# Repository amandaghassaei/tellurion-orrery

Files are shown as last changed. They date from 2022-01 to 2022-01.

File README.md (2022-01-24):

# Tellurion Orrery

This is a repository of files related to building a tellurion (Earth, Moon, and Sun) orrery from scratch.  Please refer to my [Instructables post](https://www.instructables.com/Orrery-Earth-Moon-and-Sun/) for more information about how to make this project.

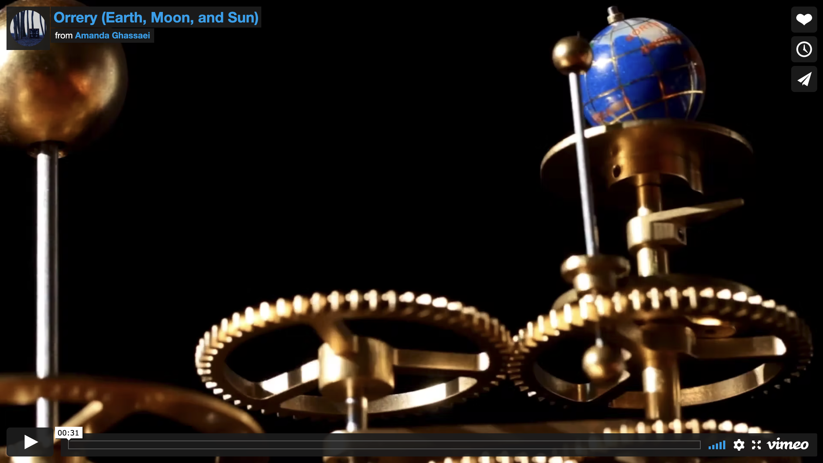
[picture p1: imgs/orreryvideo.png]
Orrery (Earth, Moon, and Sun) (https://vimeo.com/669322303 "Orrery (Earth, Moon, and Sun) - Click to Watch!")


### Repository Contents:

- [angled-jigs](angled-jigs) contains STL files for the 3D printed jigs used to cut angled holes in some parts.
- [bom](bom) contains an archived version of the bill of materials for the project, find the most up-to-date copy on [Google Docs](https://docs.google.com/spreadsheets/d/1O1LCT8TSBF-lglJqdujguVSw7xpgpI2WuT8ZgHCS0Z8/edit?usp=sharing).
- [cad](cad) contains archived versions of the cad files for the project and links to the most up-to-date versions online (see [cad/README.md](cad/README.md))
- [engravings](engravings) contains source code for generating three engravings used in the design, as well as generated DXF files.
- [gear-calculations](gear-calculations) contains information about how the mechanism was designed as well as source code for optimizing the gear ratios.
- [gear-depthing-gauge](gear-depthing-gauge) contains DXF files for laser cutting the body of the gear depthing gauge from acrylic.
- [laser-cutting](laser-cutting) contains vector files for laser cutting washers and other parts needed in the orrery design.

All files can be downloaded by clicking the green "Code" > "Download ZIP" button at the top of this page.

## License

All code and design files in this repo are free to use however you like (MIT License).

### Exceptions:

[engravings](engravings) contains a copy of [p5.js](https://github.com/processing/p5.js/), which is licensed under GNU.

[engravings/fonts](engravings/fonts) contains some fonts that likely have their own licenses associated with them.

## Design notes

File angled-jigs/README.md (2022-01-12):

## Angled Jigs

3D printed jigs for drilling angled holes in brass parts.  The most up-to-date jigs can be exported from the [CAD model](https://a360.co/3HCbeUA) (move the timeline to the end to uncover the jig designs).

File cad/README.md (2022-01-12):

## CAD Files

This directory contains archived Fusion360 files for the orrery and other associated designs; the most up-to-date CAD files can be found online:

- [Orrery v2](https://a360.co/3HCbeUA)
- [Shaft Cutting Jig](https://a360.co/3G0PzVP)
- [Gear Depthing Gauge](https://a360.co/31AS3LG)
- [Wood Cutting Layout](https://a360.co/3qWjdVE) (just a sketch, ignore warnings about empty model)

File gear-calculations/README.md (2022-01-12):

# Gear Calculations

The orrery design consists of 4 interconnected gear trains that control the relative motions of the earth, moon, and sun, and a fifth gear train that ticks forward a dial marking 100 years.

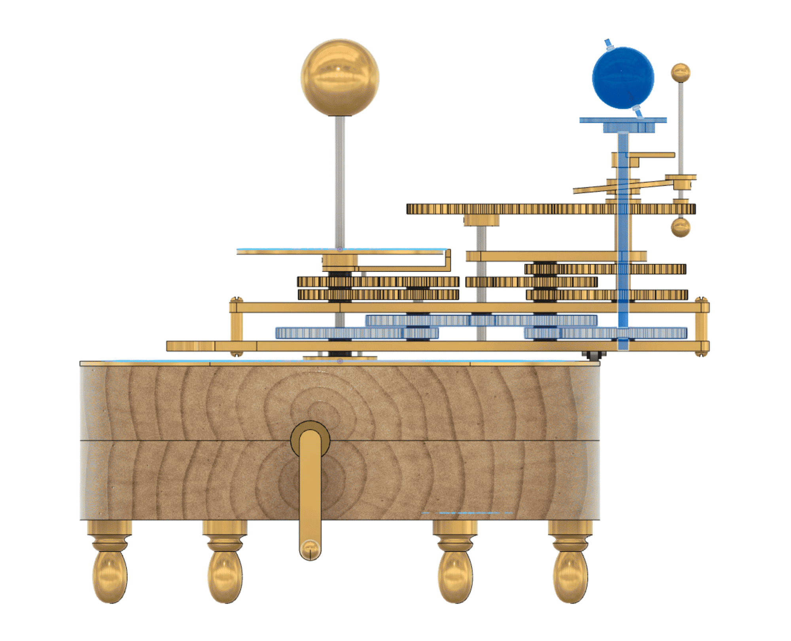
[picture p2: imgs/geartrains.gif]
5 gear trains


In addition to accurately positioning various components of the orrery, the gears must be sized so that they fit coaxially on five vertical axles:

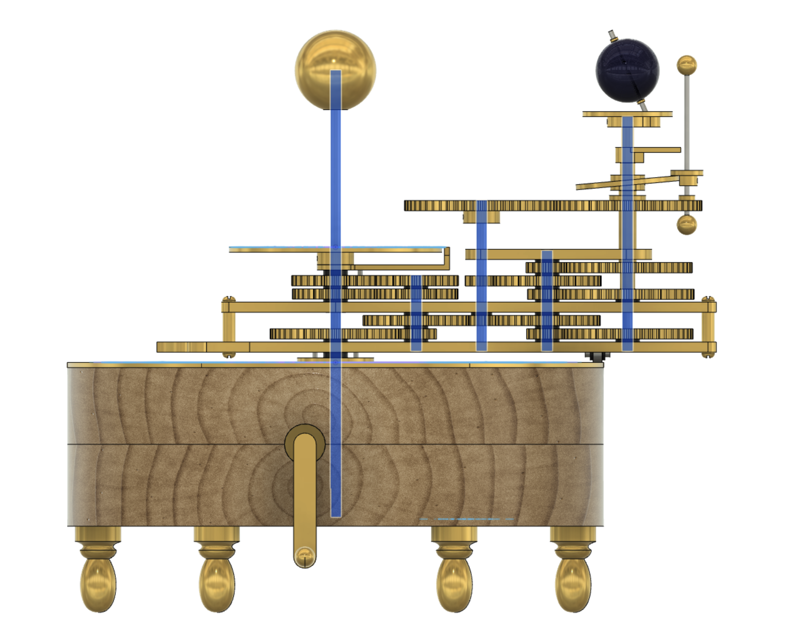
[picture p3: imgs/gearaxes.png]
gear axles


My code for calculating the gear ratios was done quickly without much thought for reuse – but I've added some notes here to explain the process.  

I've saved all the information I used during these calculations to a [Google Doc](https://docs.google.com/spreadsheets/d/1HO8HQtnuJBg7-cl2iLWuv1kIT8sFUn2m3BNM2MRiHnA/edit?usp=sharing) and I've backed up all the data in the [results](results) folder.  The first tab shows the astronomical parameters I was trying to model and their frequency.  Highlighted in blue are the gear parameters I used in v1 of my design, and highlighted in magenta are parameters used in v2 of my design.  The magenta and blue colors are continued across the other tabs in the sheet, where you can see more gear ratio options I was considering.

All the gear generation code was written in javascript and is included in this folder. I really liked this online [Gear Train app](http://scientific601.altervista.org/gear/gearcalc.html) and used it as a starting point as I began to design my gear trains, but found that I needed to calculate a large set of candidate gear trains for a given target ratio instead of just the single most optimal configuration. The file [GearCalculator.js](https://github.com/amandaghassaei/tellurion-orrery/blob/main/gear-calculations/GearCalculator.js) contains a function `calcGearTrain` that performs an exhaustive search to find set of gears meeting min tooth, max tooth, number of stages, and maximum error requirements (it takes about five minutes to complete for the three stage gear trains I'm looking at). The solutions (`hits`) are printed as a tsv to the console, so they can easily be copied and pasted into a spreadsheet.

### Moon Orbit

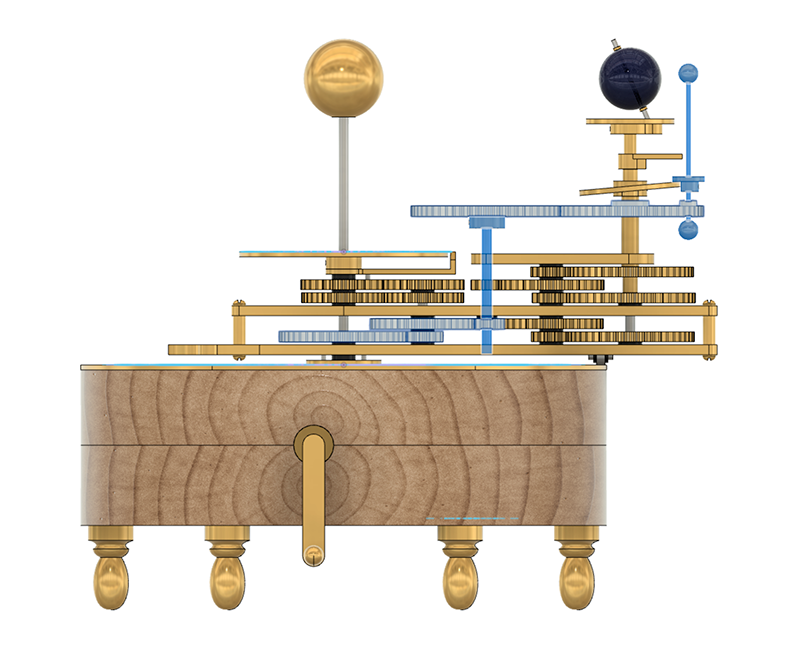
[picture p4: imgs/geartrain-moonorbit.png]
moon orbit gear train


First I used GearCalculator.js to calculate optimal solutions for a 3 stage gear train to drive the rotation of the moon around the earth. I chose a minimum tooth number of 8 and a maximum of 55. My code found the same optimal ratios as the online gear train app, but also gave me many alternatives that were slightly less optimal from an error perspective, but may satisfy other geometric properties of interest. I saved all permutations of each of these `hits` to a global variable called `options` in the file [ImportOptions.js](https://github.com/amandaghassaei/tellurion-orrery/blob/main/gear-calculations/ImportOptions.js).

[CalcFit.js](https://github.com/amandaghassaei/tellurion-orrery/blob/main/gear-calculations/CalcFit.js) uses the information stored in `options` to assess the options in terms of geometric constraints. Since I made my parts using a CNC machine, I allowed for a small amount of scaling of the tooth pitch to help open up the available gear options, but I didn't want the difference in tooth scale to be too noticeable

### Ecliptic

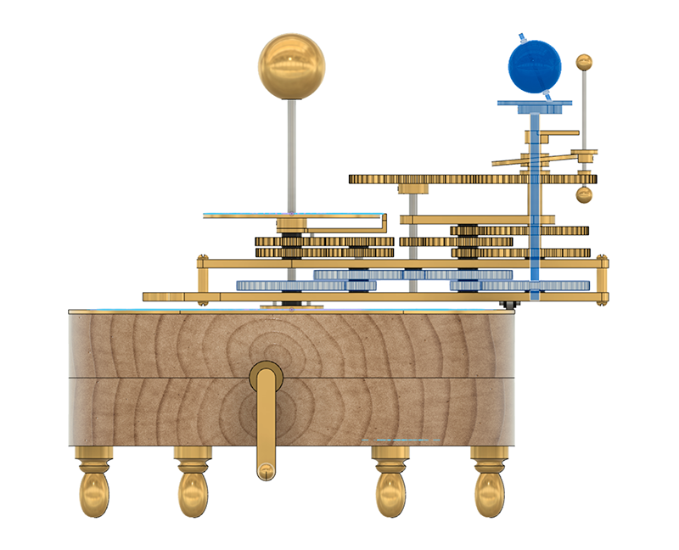
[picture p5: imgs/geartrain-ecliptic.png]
ecliptic gear train


CalcFit.js first determines the amount of scaling needed by the third stage of the moon orbit train to make it coaxial with the mirrored ecliptic train.

### Moon Nodes

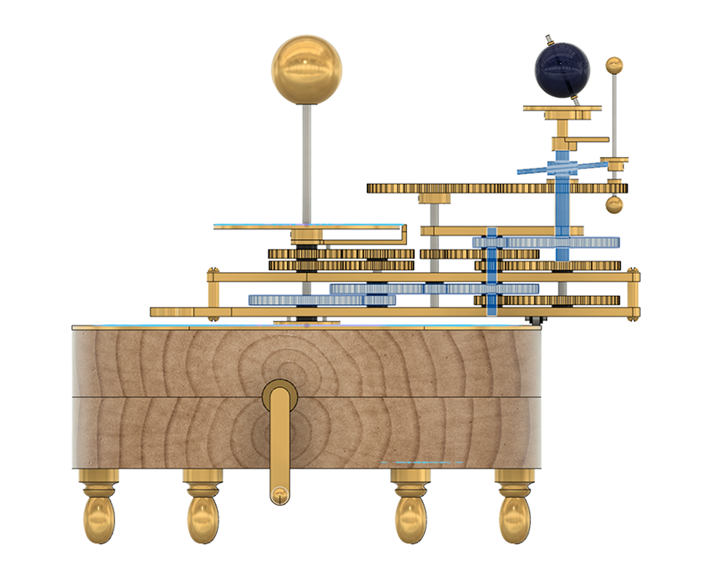
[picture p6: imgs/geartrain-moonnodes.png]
moon nodex gear train


I wanted to drive one of the remaining gear trains (either the moon's perigee or nodes) from a single stage off the fourth axle in my five axle setup, so I calculated optimal single stage trains for driving either the perigee or the nodes and printed this as a single tsv (pasted [here](https://docs.google.com/spreadsheets/d/1HO8HQtnuJBg7-cl2iLWuv1kIT8sFUn2m3BNM2MRiHnA/edit#gid=189566112) – `Gear Ratios (Moon Orbit)` tab, you have to scroll way to the right to see the perigee and nodes calculations). I found a few good options for a single stage to drive the nodes (highlighted in blue and magenta ended up using these), and another for a single stage to drive the perigee (highlighted in orange).

### Moon Perigee

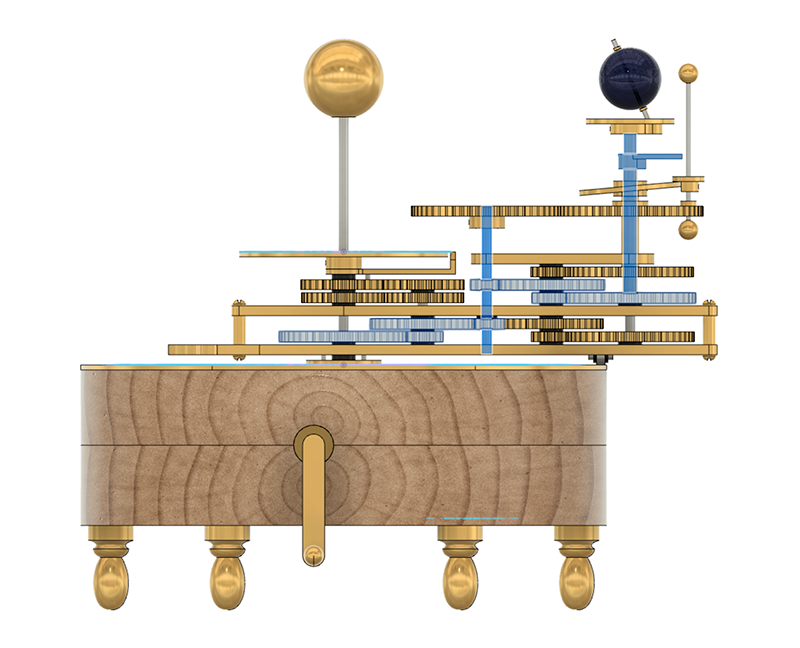
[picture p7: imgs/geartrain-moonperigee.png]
moon perigee gear train


Next I used GearCalculator.js to calculate a set of optimal 2 stage trains to be driven off the third axle of the moon orbit train. I pasted the resulting tsv [here](https://docs.google.com/spreadsheets/d/1HO8HQtnuJBg7-cl2iLWuv1kIT8sFUn2m3BNM2MRiHnA/edit#gid=854613091), [here](https://docs.google.com/spreadsheets/d/1HO8HQtnuJBg7-cl2iLWuv1kIT8sFUn2m3BNM2MRiHnA/edit#gid=1769662877), and [here](https://docs.google.com/spreadsheets/d/1HO8HQtnuJBg7-cl2iLWuv1kIT8sFUn2m3BNM2MRiHnA/edit#gid=496071409) - "Option # Gear Ratios". Again, I analyzed the spreadsheet and chose an optimal gear configuration that met my design requirements. There is no right answer here – it's a balance of aesthetics, complexity of design/manufacturing, and accuracy. I ended up choosing the solution in blue initially to minimize error and used this for version 1 of my design. Later I decided that I didn't like the large pitch scaling on one of the gear stages, so I choose the magenta option instead for version 2.  Green shows other options I was considering, but didn't make the cut.

### Year Dial

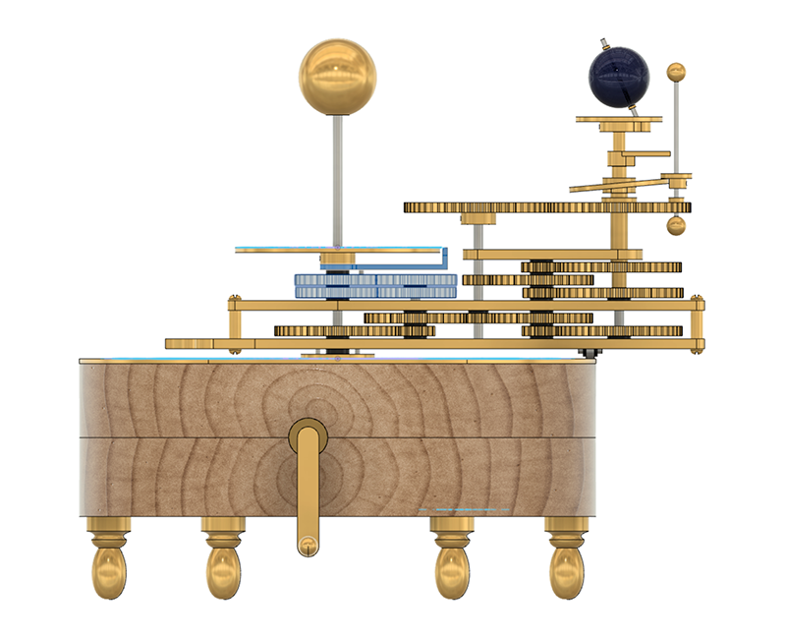
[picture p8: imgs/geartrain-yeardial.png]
year dial gear train


Finally I added a year counter that ticks over each time the arm makes one full revolution. I calculated the gear ratios for this train by hand, so that I could fit 100 years (plus some extra) in one full revolution. I ended up finding a set of gear ratios that fits 135 years on one full revolution, rotating in the same direction as the arm. I only marked off 100 years plus ten on either side.  It would have been nice to have a perfect 100 years fit on the dial, but it just wasn't possible given the geometric constraints I was working with – maybe if another stage was added, but I didn't want to introduce more complexity.

## To Edit:

This folder contains an [index.html](index.html) file where all the Javascript code is called from.

Open `index.html` in a source-code editor (I recommend [VSCode](https://code.visualstudio.com/)) and you will see the calls to `calcGearTrain` and `CalcFit`.  Hopefully the comments in there are enough to guide you.

## To Run Edited Files:

After you've edited `index.html`, you can run it by creating a local html server on your computer.

Navigate to this folder (`gear-calculations`) in the terminal and run:

`python -m SimpleHTTPServer`

Then open a web browser (I'm using Chrome) and go to:

`http://localhost:8000/`

If you don't have python installed on your machine, install node:

https://nodejs.org/en/

Then install http-server by typing the following into the terminal:

`npm install -g http-server`

After it is installed, navigate to this folder in the terminal and type:

`http-server -p 8000`

When you go to `http://localhost:8000/`, you will see an empty page.  Your browser may throw up a "Page Unresponsive" warning, just click "Wait" until the page loads.  Open up the browser's console and you will see the progress of the code (it takes a few minutes to compute each step):

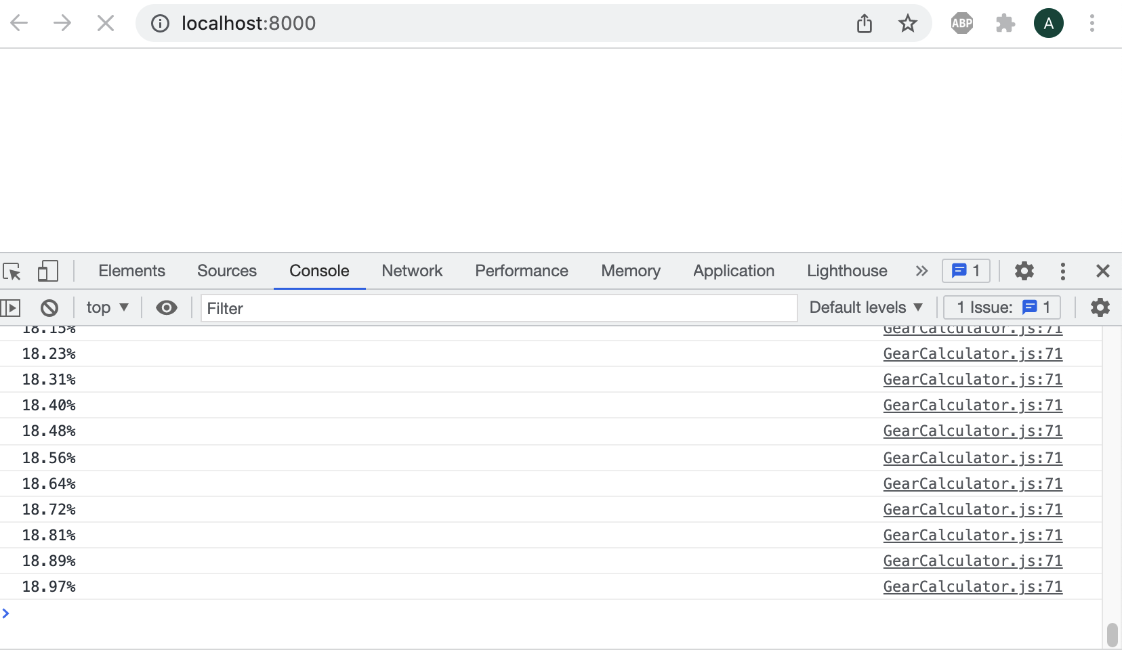
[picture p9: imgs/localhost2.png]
files at http://localhost:8000/


(Hint: try opening the console before going to `http://localhost:8000/` if the page just seems to hang for too long.)

When a computation is complete, the results will be printed in the console as tab-separated values that you can paste directly into a Google/Excel spreadsheet.

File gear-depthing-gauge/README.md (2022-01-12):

## Gear Depthing Gauge

Laser cut profiles corresponding to the gear depthing gauge [CAD model](https://a360.co/31AS3LG).  I cut these from 1/8" acrylic, DXF files have units of inches.

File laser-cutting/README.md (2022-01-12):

## Laser Cutting

DXF files have units of inches.

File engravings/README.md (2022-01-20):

# Engraving Design and Toolpathing

The engravings for the orrery were fairly complicated, so I've designed them parametrically using [P5.js](https://p5js.org/).  The scripts to generate the designs are currently hosted at the following links:

- [Calendar Engraving](https://apps.amandaghassaei.com/tellurion-orrery/engravings/CalendarEngraving.html)
- [Year Engraving](https://apps.amandaghassaei.com/tellurion-orrery/engravings/YearEngraving.html)
- [Name Engraving](https://apps.amandaghassaei.com/tellurion-orrery/engravings/NameEngraving.html)

By working parametrically, you change high level parameters in the design (like the overall dimensions, spacing of characters, length of tick marks) and generate a new layout immediately.  Here are some possible variations on my calendar design:

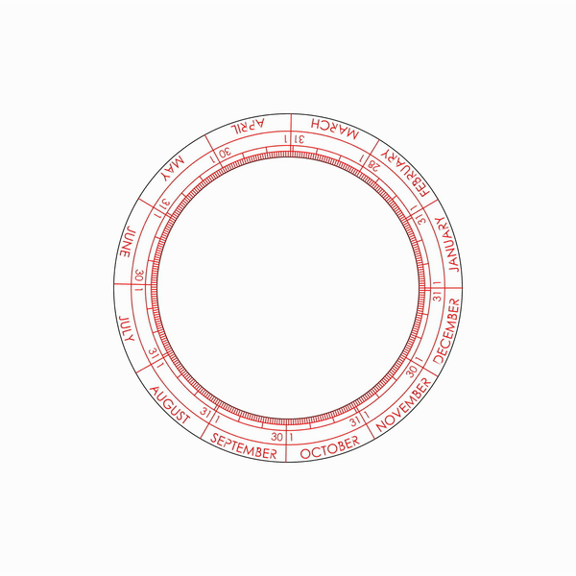
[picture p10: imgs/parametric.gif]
parametric design


The SVGs generated by my scripts will need to be converted into DXF before importing into Fusion (I did this in Illustrator).  All the DXFs included in this folder are in units of inches.

## Fonts

Currently, all scripts use the [Century Gothic](fonts/CenturyGothic.ttf) font, but you can try out the other fonts included in the [fonts](fonts/) folder, or try out your own.  I like Century Gothic for this project because it uses circles to form many of the letters, which mirrors the circular shape of the orrery overall.  Century Gothic has a thin stroke, but it is not a [single line font](http://imajeenyus.com/computer/20150110_single_line_fonts/index.shtml), so I had to edit it to make it work as an engraving font:

>A single line font is a typeface that uses one line to define the shape of each letter, or glyph. Conventional fonts utilize two lines, an inner and outer pair of lines, that define the shape and thickness of the letterforms.

The `XXX-adjusted.dxf` files in this folder show the changes I made to the font before I brought it into Fusion – once in Fusion, I added more lines to complete the letters (this was easier to do in Fusion than Illustrator because I could more easily snap to the midpoints of lines).  A single line font would not require so much editing, but I was happier with the quality of the line that I got from Century Gothic.

To give you an idea, here is what I got from [Hershey Font](https://observablehq.com/@jonsadka/hershey-vector-font-explorer) (a popular single line font):

hershey font

compared to Century Gothic:

century gothic font

There's a big difference in the quality of the curved lines (compare the `R`, `B`, and `C`).

## To Edit:

This folder contains three html files:

- [YearEngraving.html](YearEngraving.html)
- [CalendarEngraving.html](CalendarEngraving.html)
- [NameEngraving.html](NameEngraving.html)

Open each html file in this folder in a source-code editor (I recommend [VSCode](https://code.visualstudio.com/)) and you will see the javascript code used to generate each design.  Hopefully the comments in there are enough to guide you.

## To Run Edited Files:

After you've edited the files, you can run them by creating a local html server on your computer.

Navigate to this folder in the terminal and run:

`python -m SimpleHTTPServer`

Then open a web browser (I'm using Chrome) and go to:

`http://localhost:8000/`

If you don't have python installed on your machine, install node:

https://nodejs.org/en/

Then install http-server by typing the following into the terminal:

`npm install -g http-server`

After it is installed, navigate to this folder in the terminal and type:

`http-server -p 8000`

When you go to `http://localhost:8000/`, you will see links to several html files:

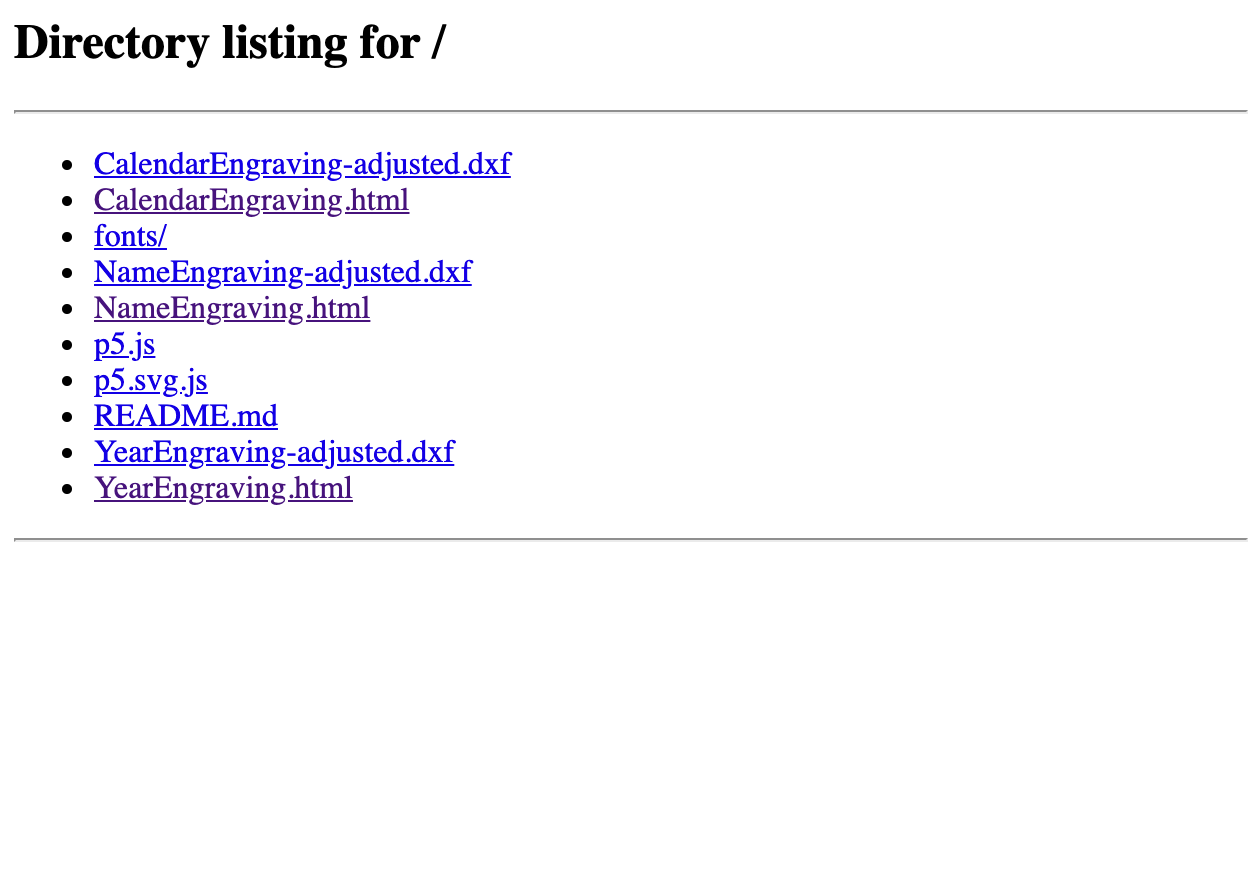
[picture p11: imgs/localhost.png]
files at http://localhost:8000/


Click on each html link and you will see your edited design drawn on the screen and the page will immediately save a copy of the design as an svg.

## Notes on Toolpathing Engravings:

The most deflection you'll get in an engraving cut happens where the tool enters the material.  Exiting the material can also leave a nonuniform surface finish.  Where possible I've extended paths to run outside the boundary of the workpiece for a better finish (these are called lead-ins and lead-outs):

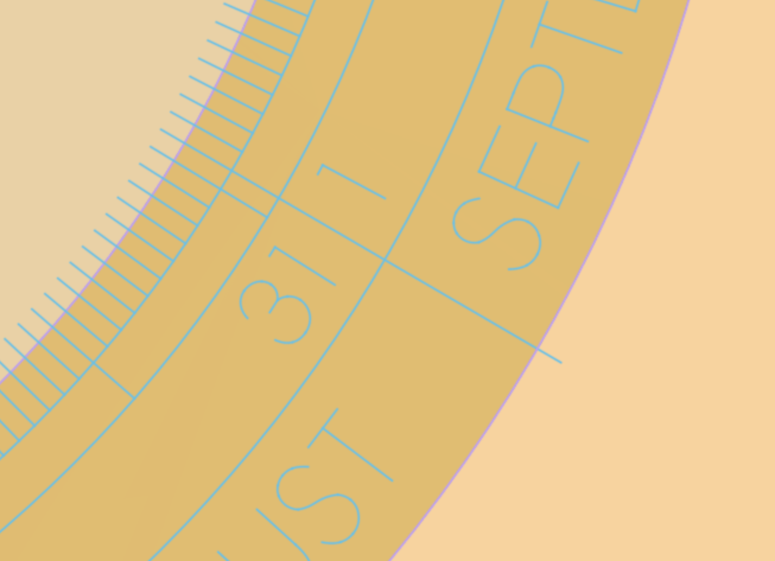
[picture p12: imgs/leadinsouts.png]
lead ins and outs


In general, you should try to minimize the number of times you enter and exit the material while you're cutting the workpiece.  So when cutting continuous paths made from several discrete line segments, be sure to select the segments in the correct order so that you generate a continuous toolpath.

These curved paths are made from several discrete line segments that must be individually selected:

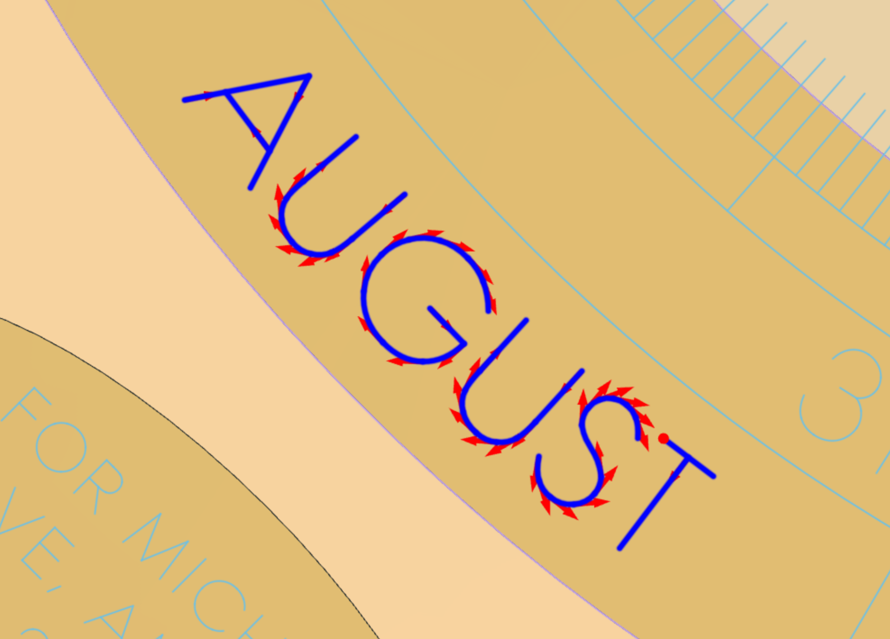
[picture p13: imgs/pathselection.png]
selecting continuous path


They have been selected in order so that they are engraved in a continuous toolpath:

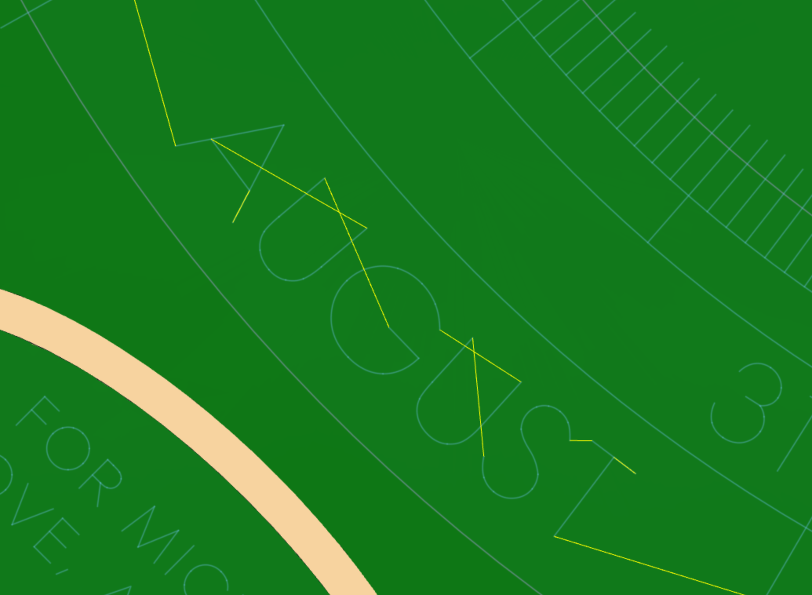
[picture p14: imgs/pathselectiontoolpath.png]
continuous toolpath


When selecting paths for engraving, you will get a more consistent result if you trace identical characters or shapes in the same direction each time.  So if you have several of the character `T` in your design, pick a direction to traverse the contours of the `T` and be consistent across the toolpath.  Similarly, all tickmarks should be traversed in the same direction.

See how the `E` character is traversed in the same way in this toolpath:

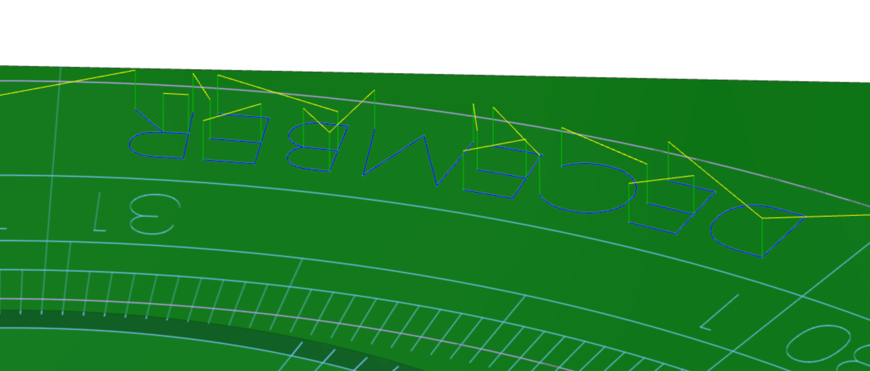
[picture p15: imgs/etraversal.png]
character traversal


These tick marks are also traversed in a consistent direction:

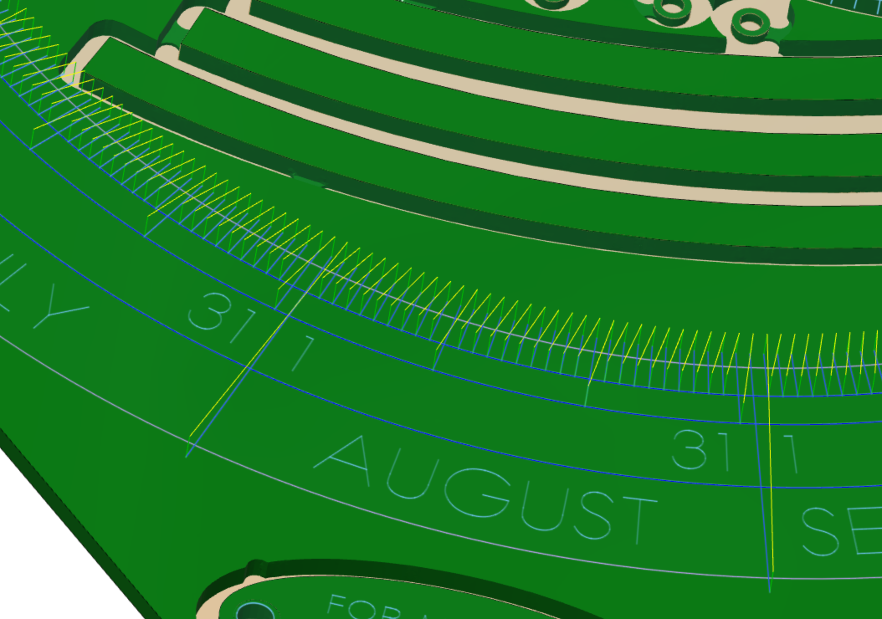
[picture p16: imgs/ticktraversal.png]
tick traversal


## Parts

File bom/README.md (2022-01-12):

## Bill of Materials

The most up-to-date bill of materials can be found on [Google Docs](https://docs.google.com/spreadsheets/d/1O1LCT8TSBF-lglJqdujguVSw7xpgpI2WuT8ZgHCS0Z8/edit?usp=sharing), archived here as a backup.

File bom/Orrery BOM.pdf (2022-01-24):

Part Name | Vendor | SKU | Unit Cost | Quantity | Total Price | Num Per Container | Num Used | Notes

*note that I get a small commission off these Amazon links, but this is
where I buy a lot of my supplies anyway.
I recommend checking your local hardware store first, as many of these materials are available there, consider these links more of a reference

than a specific brand requirement.

Brass Stock
3/16" 360 brass 4" x 6" sheet (https://www.mcmaster.com/8954K412-8951K868/) | McMaster-Carr | 8954K412 | $36.16 | 1 | $36.16
1/8" 360 brass 4" x 12" sheet (https://www.mcmaster.com/8954K149-8954K349/) | McMaster-Carr | 8954K149 | $47.76 | 1 | $47.76
0.5" diameter x 6" 360 brass round stock (https://www.mcmaster.com/8953K174-8953K175/) McMaster-Carr | 8953K174 | $16.42 1 $16.42 Only about 1.5" of this is needed for cutting shaft collars.
0.063" 353 brass sheet 6" x 6" sheet (https://www.mcmaster.com/8956k175) Silver-Toned Metal Shim (optional) | McMaster-Carr 8956K175 $33.31 1 $33.31 | McMaster does not sell 360 ultra machinable brass in thinner sheets. I used the 353 brass instead, it is also very machinable.
n/a – you will only need a tiny scrap of silver colored metal | source locally | | $0.00 | 1 | $0.00 | This is to add a silver tooth to the calendar dial to mark a special date. Use a piece of scrap. I used aluminum.

Steel Rod
1/16" OD tight tolerance stainless steel rod 6" length (https://www.mcmaster.com/88915K11-88915K119/) | McMaster-Carr | 88915K11 | $3.54 | 1 | $3.54 | Only a few inches needed. Brass also available.
1/8" OD tight tolerance stainless steel rod 12" length (https://www.mcmaster.com/8934K24-8934K242/) | McMaster-Carr | 8934K24 | $7.84 | 2 | $15.68 | I think it's worth it to pay the extra for tight-tolerance on these rods - makes the press fits more reliable and saves some filing work later, but McMaster also sells a standard
| | | | | | tolerance version of these rods for 1/3 the price. Brass also available, though I ended up liking the look of the mixed metals more.

Brass Tubes
*Note from McMaster: Tubes with 0.014" and 0.45 mm wall thicknesses allow you to create telescoping tubes; each tube fits inside the next larger size. I went with imperial sizes because McMaster tends to have more inventory in inches than mm that would be compatible with the tubes. **These brass tubes are used widely and can often be found at the local hardware/craft store. Some interesting ideas about working this these tubes here: http://steampunkworkshop.com/making-joints-telescoping-brass-tubing-slip-fit-press-fit-detent-fit/
***McMaster does not sell tubes in the 360 brass. The 260 brass has a
slightly different color than the 360, but it is not very noticeable.
5/32" OD 0.128" ID brass tube (https://www.mcmaster.com/#8859k21/=19sx6qv) | McMaster-Carr | 8859K21 | $2.12 | 1 | $2.12 | Only a few inches needed.
3/16" OD 0.16" ID brass tube (https://www.mcmaster.com/8859K22/) | McMaster-Carr | 8859K22 | $2.08 | 1 | $2.08 | Only a few inches needed.
7/32" OD 0.191" ID brass tube (https://www.mcmaster.com/8859K23/) | McMaster-Carr | 8859K23 | $2.61 | 1 | $2.61 | Only a few inches needed.

Aluminum Rod
3/8" OD 6061 aluminum rod 6" length (https://www.mcmaster.com/8953K124-8953K125/) | McMaster-Carr | 8974K24 | $1.25 | 1 | $1.25 | Only a few inches needed, used for central drive. A 1/4" rod would also work, but was too small for my lathe chuck.

Thrust Washers
*I laser cut this stock to the correct washer sizes I needed. Double thick washers in the CAD model are made from two layers of washers.

**These washers could be made out of anything (like standard metal washers), it's not critical to be low friction because the parts of this
machine don't move that fast - laser cutting them myself was cheaper and
easier for me because I could control the size.
Delrin 0.031 strip film black 5ft (https://www.mcmaster.com/2638T21/) | McMaster-Carr | 2638T21 | $3.55 | 1 | $3.55 | Only about a foot needed.

Bearings
10 pack bearing for 1/8" shaft with 1/4" OD and 7/64" height (https://amzn.to/3vk7dOY) | Amazon | | $10.89 | 2 | $21.78 | 10 | 13 These bearings are $1 each on Amazon - since this isn't a high performance application, I don't care about quality too much. If Amazon is not an option for you, the bearings could be subbed with these (much more expensive) bearings from McMaster.
thrust bearing 0.5" shaft, 15/16" OD (https://www.mcmaster.com/5909K31/) | McMaster-Carr | 5909K31 | $3.91 | 1 | $3.91
0.032" washer for 0.5" thrust bearing (https://www.mcmaster.com/5909K44/) | McMaster-Carr | 5909K44 | $1.23 | 1 | $1.23

Screws/Bolts
*you should check out your local hardware store first to see if you can
buy these screws individually, as very few per pack are used.
M2 2mm stainless steel set screws (https://www.mcmaster.com/92015A011/) | McMaster-Carr | 92015A011 | $7.50 | 1 | $7.50 | 25 | 1 Tiny screw for the moon shaft collar, you could also file down a 4mm screw to achieve this.
M2 4mm stainless steel set screws (https://www.mcmaster.com/92015A090/) | McMaster-Carr | 92015A091 | $5.98 | 1 | $5.98 | 25 | 4 Shaft collar sets screw for various parts.
M2.5 4mm stainless steel set screws (https://www.mcmaster.com/92015A095/) | McMaster-Carr | 92015A095 | $8.29 | 1 | $8.29 | 50 | 3 Set screws for the two shaft collars that were turned on the lathe and the crank handle. M2 screws would work here too, but the M2.5 have more grip.

Part Name | Vendor | SKU | Unit Cost | Quantity | Total Price | Num Per Container | Num Used | Notes
M3 5mm stainless steel set screws (https://www.mcmaster.com/92015A103/) | McMaster-Carr | 92015A103 | $8.68 | 1 | $8.68 | 50 | 1
| | | | | | | | Used for the bottom mount on on the central axis, a smaller screw would work here (e.g. M2.5), but the M3 are better if you can swing it.
M3 12mm stainless steel set screws (https://www.mcmaster.com/92015A107/) | McMaster-Carr | 92015A107 | $12.20 | 1 | $12.20 | 50 | 3 Used for crank adjustments (inside threaded inserts). This is an odd part bc it is so long, you can also use regular M3 bolt, but you'll have to figure out how long you need based on your setup
1/4-20 stainless set screw 3/8" length, 1/8" drive size (https://www.mcmaster.com/94355A535/) | McMaster-Carr | 94355A535 | $4.66 | 1 | $4.66 | 25 | 1 For sun attachment to central shaft.
6-32 brass set screw 1/8" length, 1/16" drive size (https://www.mcmaster.com/92991A142/) | McMaster-Carr | 92991A142 | $4.94 | 1 | $4.94 | 50 | 2 For moon and counterweight attachment.
M3 threaded inserts (https://www.mcmaster.com/95807A490/) | McMaster-Carr | 95807A490 | $2.73 | 3 | $8.19

These screw into the wood base for adjustment mechanism for worm gear meshing alignment. I found needed to install these in a slightly larger hole than recommended on McMaster's website.

2-56 1/4" decorative round head brass screws (https://www.mcmaster.com/92453A077/) | McMaster-Carr | 92453A077 | $5.18 | 1 | $5.18 | 100 | 6 McMaster's brass standoffs have a zinc coating, so I'm just using the smallest, cheapest metal standoffs available. For the final finish, I've added a bit of brass tube around the
| | | | | | | standoff.
#2 1/4" decorative round head brass wood screws (https://www.mcmaster.com/92407A077/) | McMaster-Carr | 92407A077 | $5.19 | 1 | $5.19 | 100 | 2 For mounting the nameplate to the underside of the wood base.

1/8" diameter 3/8" tall 2-56 threaded aluminum standoffs (https://www.mcmaster.com/93330A252/) | McMaster-Carr | 93330A252 | $1.09 | 3 | $3.27 | | McMaster's brass standoffs have a zinc coating, so I'm just using the smallest, cheapest metal standoffs available. For the final finish, I've added a brass tube around the standoff.
M2 4mm brass slotted screws (https://www.mcmaster.com/96686A363/) | McMaster-Carr | 96686A363 | $12.50 | 1 | $12.50 | 50 | 2

For attaching the moon orbit cam to its mount (these will need to be shortened a little bit, but McMaster does not carry shorter lengths). I would have liked to use a decorative round head screw for this, but had trouble sourcing.
#4 3/4" square drive stainless steel screws (https://www.mcmaster.com/94155A096/) | McMaster-Carr | 94155A096 | $6.72 | 1 | $6.72 | 100 | 9 9 used for final assembly, also used about 20 screws to fixture 1/8" and 3/16" brass stock for machining. The important thing about these screws is that they will fit inside an 1/8" hole without damaging the surface finish. The square drive prevents stripping.

1.5" wood screws (https://www.mcmaster.com/90031A203/) | McMaster-Carr | 90031A203 | $5.28 | 1 | $5.28 | 100 | ~5 Only for fixturing, not used for final assembly.

Dowel Pins
*convenient but optional, these could be made from the 1/16" rod
1/16" stainless steel dowel pins 1/4" long (https://www.mcmaster.com/90145A415/) | McMaster-Carr | 90145A415 | $9.91 | 1 | $9.91 | 100 | 5

Base / Feet / Crank
hardwood 5/4"x4"x30" | source locally | | $15.00 | 1 | $15.00 | | I used domestic cherry.
1/8" acrylic sheet 6" x 12" (https://www.mcmaster.com/8560K275/) | McMaster-Carr | 8560K275 | $5.70 | 1 | $5.70 | | Only a few square inches needed. Not visible from the outside, any color is fine. Also used for gear depthing gauge (see below).
1/8 IPS unfinished brass finial (https://grandbrass.com/1-8ips-9-16in-x-1in-acorn-finial-unfinished-brass/) | Grand Brass Lamp Parts | FI669 | $1.50 | 6 | $9.00 | | Many other styles available, should be at least 1" in height.
3/4" steel nipple 1/8 IPS (https://grandbrass.com/3-4in-x-1-8ips-threaded-zinc-plated-steel-hollow-nipple/) | Grand Brass Lamp Parts | NI0-3/4X1/8 | $0.10 | 6 | $0.60
shaft collar 1/8" ID, 3/8" OD, 1/4" wide (https://www.mcmaster.com/9414T3/) | McMaster-Carr | 9414T3 | $1.23 | 1 | $1.23
size 0 brass vienna clock crank (http://www.rnhorological.co.uk/clock%20and%20watch%20keys.htm) | R&N Horological | T-S 941 | $5.19 | 1 | $5.19
30:1 worm gear set 3mm diameter (https://amzn.to/3FaHInl) | Amazon | | $17.28 | 1 | $17.28 | | Order early, may ship from china. Will need to bore the worm wheel out to 1/4" ID. This 40:1 worm drive could also be nice, but 3D model will need to be adjusted.
3mm x 10mm x 0.3mm compression springs (https://amzn.to/3z8VpAG) | Amazon | | $6.99 | 1 | $6.99 | 10 | 6 Stiffer option: 3mm x 10mm x 0.5mm compression spring

Earth
*These inlaid beads vary a lot in quality, so take a close look at the
pictures before ordering, I found a really nice one on AlphaStamps, but it doesn't look like they are selling this part anymore.
**I liked the slightly abstract representation of Earth that I got from these
handmade globe beads, but if you want something more realistic, you
could have one 3D printed on Shapeways.
20mm earth beads | multiple sources (see note) | | $12.00 | 1 | $12.00 | | These can be sourced from Etsy, John F Allen, and ZnetShows (among other places), note that the quality varies greatly from source to source.

Moon and counterweight
1/4" diameter, 6-32 threaded brass ball (https://amzn.to/3c7GJZl) | Amazon | | $7.54 | 1 | $7.54 | 10 | 2

Sun
1" brass ball with 1/4"-20 threaded hole (https://www.mcmaster.com/60215K55/) | McMaster-Carr | 60215K55 | $7.10 | 1 | $7.10

Magnet Fasteners (optional)
In case you don't want to epoxy the calendar dial to the wood base, an
option is to fasten it magnetically.
8mm x 3mm neodymium magnets (optional) | Amazon | | $7.99 | 1 | $7.99 | 50 | 6
0.018" 430 stainless steel 0.5" x 12" strip (optional) | McMaster-Carr | 8457K44 | $0.99 | 1 | $0.99 | | This is cut into small pieces and epoxied to the backside of the brass calendar plate to attach it to the magnets
Parts Total | $396.50 <<< $100 dollars of that is for screws, of which you only use a few $ worth, I recommend buying screws individually to cut costs.

Tools

Part Name | Vendor | SKU | Unit Cost | Quantity | Total Price | Num Per Container | Num Used | Notes
1/8" upcutter end mill (for metal) (https://amzn.to/3fKCML9) | Amazon | $22.50 | 1 | $22.50 | 5 | 1
| | | | | | | | I would have liked to use a 2 flute cutter for better chip clearance, but these were really cheap and I've been happy with their performance.
1/16" 2 flute upcutter end mill (>1/8" length of cut) (for metal) (http://www.carbidedepot.com/00625in-DIA-2FL-SE-AlTiN-116-P180145.aspx) | Carbide Depot | CU 130007 | $8.79 | 1 | $8.79
3/64" 2 flute upcutter end mill (1/8" length of cut) (for metal) (http://www.carbidedepot.com/Product.aspx?ProductId=180144) | Carbide Depot | CU 129996 | $10.34 | 1 | $10.34 | Get extras, these are easy to break.
1/32" 2 flute upcutter end mill (1/8" length of cut) (for metal) (http://www.carbidedepot.com/00312in-DIA-2FL-SE-AlTiN-132-P180143.aspx) | Carbide Depot | CU 129985 | $12.14 | 2 | $24.28 | Get extras, these are very easy to break.
30deg v-bit engraver (https://amzn.to/3ECZOyI) | Amazon | $12.99 | 1 | $12.99 | 10 | 1 The tip breaks when cutting into brass with these, but it still works.
1/4" 2 flute downcutter end mill (for wood) (https://amzn.to/3urj9xe) | Amazon | $19.54 | 1 | $19.54
1/4" 2 flute upcutter end mill (for wood) (https://amzn.to/3e75aqy) | $15.95 | 1 | $15.95
1/8" 2 flute downcutter end mill (for wood) (https://amzn.to/2TibpAF) | Amazon | $18.04 | 1 | $18.04
1/4" 2 flute ball nose end mill (for wood) (https://amzn.to/3yBgRyL) | Amazon | $15.43 | 1 | $15.43
center drill set (https://amzn.to/34g9rTt) | source locally | $13.99 | 1 | $13.99
| | | | | | | | I have this metric one because I tend to use metric screws in other projects, exact sizes don't really matter.
fractional drill index (increments of 1/64) (https://www.mcmaster.com/8907A12/) | McMaster | 8907A12 | $31.13 | 1 | $31.13 | At some point I'd like to modify this set to work better for brass.
90 deg countersink (optional) | McMaster-Carr | 2742A28 | $17.41 | 1 | $17.41

Optional - I used this to add a slight chamfer to some holes before press fitting, reaming, or opening up the holes to a larger diameter. I just held the tool in my hand to do this chamfering very lightly. You can also use the tip of a large drill bit for this.
1/8" undersized reamer (https://www.mcmaster.com/3087A51/) | McMaster-Carr | 3087A51 | $12.61 | 1 | $12.61
M2, M2.5, M3 taps (https://amzn.to/3yx7hwR) | Amazon | $16.99 | 1 | $16.99

I got this set from Amazon, you can use the 1/16" drill to make the hole for the M2 threads (1/16 ~= 1.6mm), the M2.5 requires a 2.0mm drill, M3 requires a 2.5mm drill. I got the smaller drill sizes from this pin vise set (the pin vise also comes in handy for this project).

M2 bottoming tap (optional) | McMaster | 26475A63 | $21.41 | 1 | $21.41

Optional – I found that I needed this tap for the moon shaft collar (the smallest part), where there was very little clearance to cut threads. You could also tap all the way through the part or use Loctite 603 here to bond the shaft collar to the shaft and avoid buying another tool.
small tap handle (https://amzn.to/3mmGs9Z) | Amazon | | $11.00 | 1 | $11.00 | I haven't used this part from Amazon specifically, but it seems like it would work. You'll need tap handles that go down to M2, which is somewhat unusual. I like these types of tap handles because I can drill a small center hole in the top and use the tap guide to center the tapping on the mill or drill press.
tap guide (optional) | Amazon | | $8.95 | 1 | $8.95 | Optional I find these handy.
edge finder (https://amzn.to/3fmjeh2) | Amazon | | $17.73 | 1 | $17.73
center punch tool (https://amzn.to/3qbmCQ7) | | | $12.99 | 1 | $12.99 | You can also use a sharp nail and hammer for the same effect.
angle/wire cutters (https://amzn.to/3qcFFsY) | source locally | | $7.06 | 1 | $7.06 | For cutting tabs on brass stock.
#0 square drive (https://amzn.to/34uKqEt) | source locally | | $3.99 | 1 | $3.99

small flathead screwdriver (like one from this set) | source locally | | $5.99 | 1 | $5.99
needle files (https://amzn.to/2SpoPKO) | Amazon | | $7.99 | 1 | $7.99
larger metal file (https://amzn.to/3z0f4n8) | Amazon | | $7.97 | 1 | $7.97
imperial hex key set (https://amzn.to/2SIrqzk) | source locally | | $11.64 | 1 | $11.64
metric hex key set (https://amzn.to/3oQebcb) | source locally | | $11.64 | 1 | $11.64
M0.9 hex key (https://www.mcmaster.com/7289A32/) | McMaster | 7289A32 | $0.29 | 1 | $0.29 | For driving M2 set screws.
lathe cutting tool (https://amzn.to/32ooNrh) | | | $10.00 | 1 | $10.00 | Something like this - you will need to find something that fits in your setup.
lathe parting tool (https://amzn.to/2TRjiNO) | Amazon | | $20.00 | 1 | $20.00 | Something like this - you will need to find something that fits in your setup.
tumble polisher (https://amzn.to/3fkj3SI) | Amazon | | $66.99 | 1 | $66.99 | I have a Lortone tumble polisher, but this looks similar.
2lbs tumble polisher stainless steel shot media (https://amzn.to/31SzFxX) | Amazon | | $22.95 | 1 | $22.95
digital calipers (https://amzn.to/3wCxsAv) | Amazon | $25.99 | 1 | $25.99

Obviously there are much nicer calipers out there, but if you're just starting, I'd recommend getting something you won't have to worry about too much if you accidently drop.

digital micrometer (https://amzn.to/3flYCpy) | Amazon | | $39.99 | 1 | $39.99

Obviously there are much nicer micrometers out there, but if you're just starting, I'd recommend getting something you won't have to worry about too much if you accidently drop.

Knurlmaster Standard Kit hand knurler (optional, but handy) | Eagle Rock Technologies | K1-207-10-H | $188.70 | 1 | $188.70

I ordered this with the fine tooth straight knurls installed instead of the regular straight knurls.
butane torch (https://amzn.to/3fkMeoW) | source locally | $10.00 | 1 | $10.00 | For melting engraver's wax, get one prefilled with butane.
strap clamps (https://amzn.to/3IJCTEG) | Amazon | $13.57 | 2 | $27.14 | For glueing up wood base, it's also possible to use regular clamps for this.
Gear Depthing Gauge | This is a tool that will need to be made to help accurately position the gear axes.
This is a very simple (and probably much less accurate) version of
Clickspring's tool described here.
In addition to the parts listed here, I also used some of the acrylic for the
body of the gauge and some of the 1/8" stainless rod (filed to be a slip fit
in the undersized gear holes). These materials are listed elsewhere in
the BOM.
vented screw 1" long, 1/8" vent diameter (https://www.mcmaster.com/90220A210/) | McMaster-Carr | 90220A210 | $9.30 | 2 | $18.60
corresponding nut (https://www.mcmaster.com/92673A137/) | McMaster-Carr | 92673A137 | $2.68 | 1 | $2.68 | 10 | 2

Part Name | Vendor | SKU | Unit Cost | Quantity | Total Price | Num Per Container | Num Used | Notes
long M3 screw | source locally | | $1.50 | 1 | $1.50 | | 1

This is a fine-tune adjustment screw for the gauge, aim for 30-50mm in length. You will probably never use a screw with these dimensions again, so I recommend going to the local hardware store and buying the longest single M3 you can get rather than a whole box, I got a 30mm socket head screw.
M3 nut (https://www.mcmaster.com/98676A100/) | McMaster-Carr | 98676A100 | $5.39 | 1 | $5.39 | 100 | 1
Tools Total | | | | | $808.57

Consumables
Loctite 603 (https://www.mcmaster.com/91458A340/) | McMaster | 91458A340 | $16.84 | 1 | $16.84
Tap Magic cutting oil (https://amzn.to/3bSx09g) | source locally | $10.00 | 1 | $10.00 | For tapping and reaming.
SuperLube synthetic grease (https://amzn.to/3BatAs8) | Amazon | $4.98 | 1 | $4.98 | For final assembly.
Pure Tung Oil | source locally | | $10.00 | 1 | $10.00
clear lacquer spray (https://amzn.to/3eJjfLe) | Amazon | $19.99 | 1 | $19.99

I really liked this Mohawk ultra flow lacquer spray in clear gloss. I actually used the satin finish for most of my parts, but would go for glossy next time since you can bring it to a satin finish with 0000 steel wool. I did use the ultra flow gloss finish on the engravings and was very happy with the results after about 3 coats. Other brands I saw recommended were Nikolas and Staybrite. I went with the aerosol spray for convenience, but many suggest dipping in thinned lacquer for better results (so far I have not figured out a good strategy for doing this). If you don't want to use lacquer, you might check out Renaissance Wax.
odorless mineral spirits | source locally | $10.00 | 1 | $10.00
acetone | source locally | $10.00 | 1 | $10.00 | Don't use acetone on the engravings, it will melt the wax!
white vinegar | source locally | $1.00 | 1 | $1.00 | The acid reacts with the surface of the brass to remove oxidation and give it a whiter appearance. Some recommend lemi shine for this, I found that the white vinegar works just as well.
polishing cloth | source locally | $5.00 | 1 | $5.00 | Cutting up an old cotton t-shirt works.
0000 steel wool (https://amzn.to/3FOimgd) | source locally | $5.00 | 1 | $5.00 | For applying a fine brushed finish to brass.
multiple grit wet/dry sandpaper (for metal) | source locally | $9.99 | 1 | $9.99 | Use this wet to reduce dust.
multiple grit sandpaper (for wood) (https://amzn.to/3p4Qf4I) | source locally | $2.28 | 1 | $2.28 | I use the lighter color sandpaper on wood so it doesn't leave any black oxides on my piece.
orbital sanding pads | source locally | $5.00 | 1 | $5.00
black engraver's wax (https://timesavers.com/i-8947850-black-dial-wax.html) | Timesavers | $12.50 | 1 | $12.50

For darkening the letters on the dial - I originally tried using jax black patina, but didn't end up getting a dark enough result. Another source for the wax that I believe would be comparable is a "lacquer burn in stick": https://www.lmii.com/fretting-setup-tools/3051-burn-in-lacquer-stick-black-34-oz.html
scotch double sided tape (https://amzn.to/3IEsjP8) | source locally | $2.00 | 1 | $2.00 | I like using scotch tape, stronger tapes may make your workpiece too difficult to remove.
painter's/masking tape (https://amzn.to/34xbJxH) | source locally | $3.00 | 1 | $3.00
dawn dish soap (the blue one) | source locally | $3.00 | 1 | $3.00 | For tumble polishing.
1"x6"x12" HDPE spoilboard (https://www.mcmaster.com/8619K851/) | McMaster-Carr | 8619K851 | $23.01 | 1 | $23.01

I screwed down the brass to this to fix it in the vise during machining. I'm able to resurface this same piece and use it again for many projects, amortizing the cost.
epoxy | source locally | $5.00 | 1 | $5.00
Consumables Total | $158.59

Large Machines / Power tools

3 axis CNC mill - I used a Tormach PCNC 1100

Since this project uses very small bits, a high RPM spindle is better (though you will need the option to slow down to about 2K RPM for some of the reaming/drilling operations). The machine I used only went up to about 6k; I think I could have gone a lot faster with a higher RPM machine.

3 axis CNC mill (for cutting wood) – I used a Shopbot PRS Alpha

I can't cut wood on the Tormach because of the coolant system, so I used the Shopbot instead.

manual mill

Not strictly necessary, but it was useful drilling/tapping and for facing off some of my parts when the stock was a bit too thick.

lathe

There are two brass shaft collars and a thick-walled aluminum tube that had to be made for this project. Theoretically, they could also be made on the CNC.

3d printer

For making jigs for drilling angled holes in Earth mount and moon cam shaft collar. The angled holes could be cut without the jigs with a bit more effort.
bandsaw | For cutting rod/tube stock.
disc/belt sander | For dimensioning rod/tube stock, removing tabs from gears.
small arbor press | For pressing together press fit joints.
tablesaw | For cutting wood pre-glueup.
drum sander | For planing wood post-glueups.
cordless drill
orbital sander

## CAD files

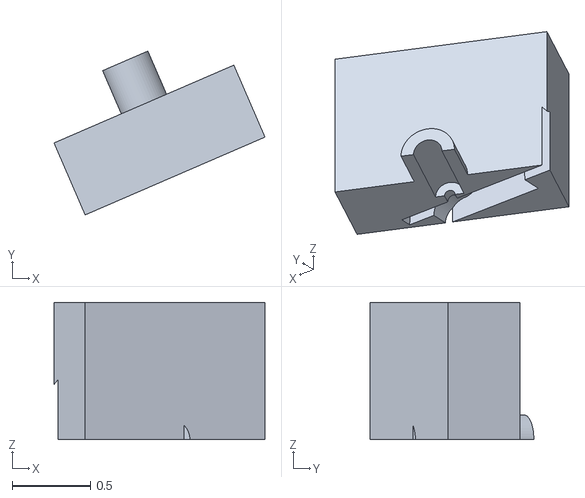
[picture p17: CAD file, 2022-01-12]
angled-jigs/earth_jig_side_2.stl
1.35 x 1.04 x 0.875

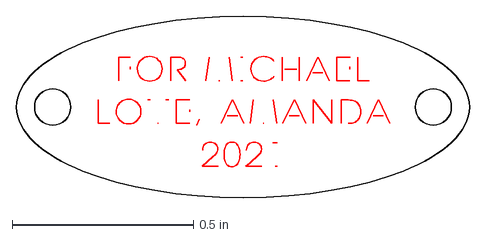
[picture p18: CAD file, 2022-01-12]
engravings/NameEngraving-adjusted.dxf
1.25 x 0.5 in

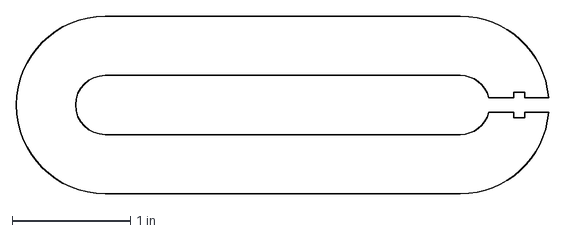
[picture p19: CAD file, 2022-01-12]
gear-depthing-gauge/Profile 2 (X1).dxf
4.50 x 1.50 in

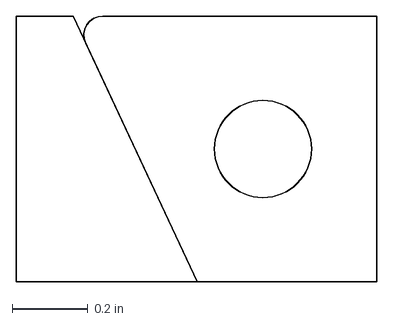
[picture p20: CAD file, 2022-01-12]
laser-cutting/acrylic_sliding_mechanism_profile_X3.dxf
0.95 x 0.7 in

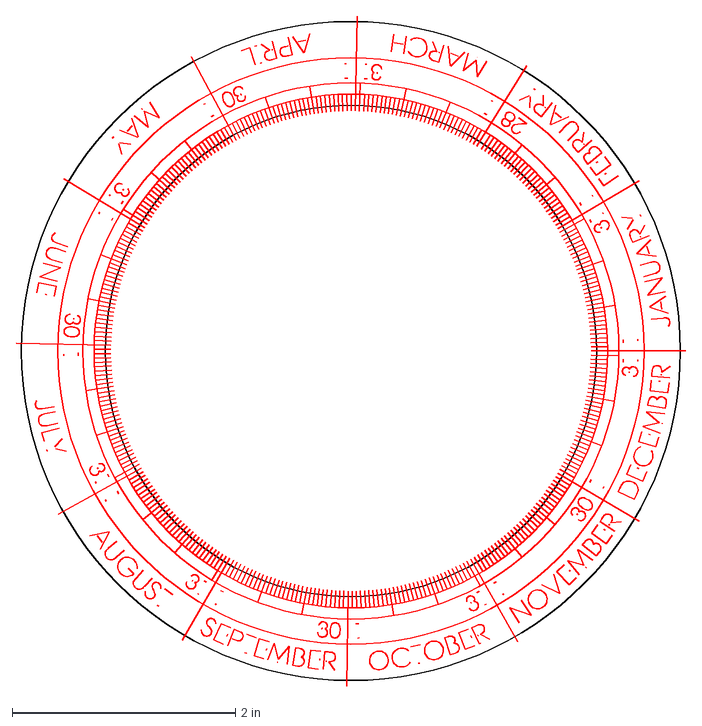
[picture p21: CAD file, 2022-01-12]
engravings/CalendarEngraving-adjusted.dxf
6.00 x 6.00 in

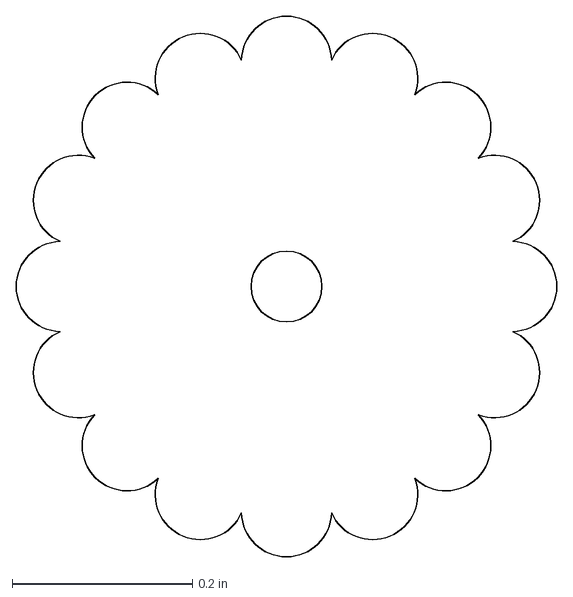
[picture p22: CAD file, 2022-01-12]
gear-depthing-gauge/Profile 3 (X1).dxf
0.6 x 0.6 in

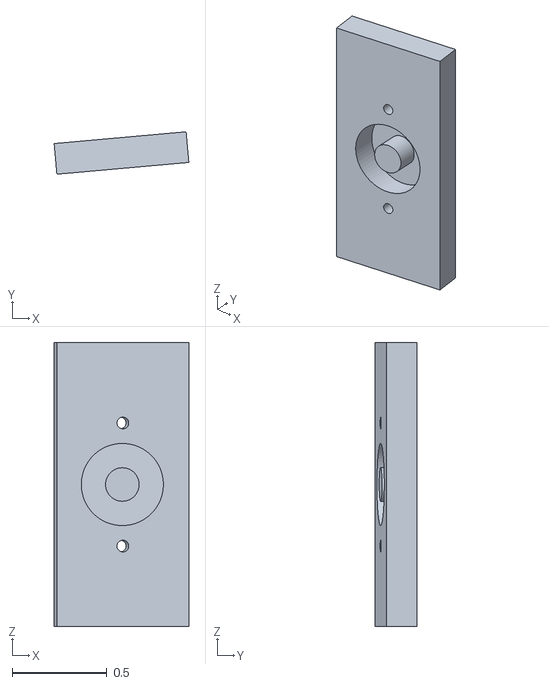
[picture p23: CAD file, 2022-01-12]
angled-jigs/moon_jig_side_1.stl
0.712 x 0.224 x 1.50

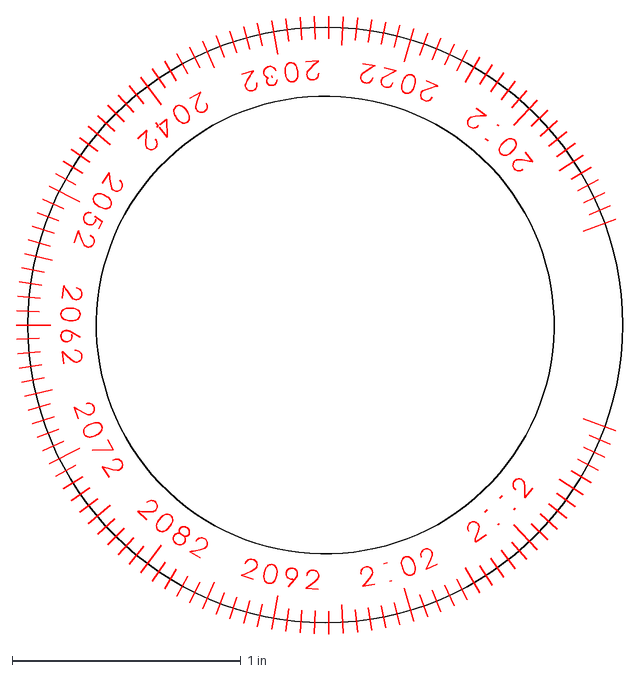
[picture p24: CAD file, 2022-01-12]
engravings/YearEngraving-adjusted.dxf
2.65 x 2.70 in

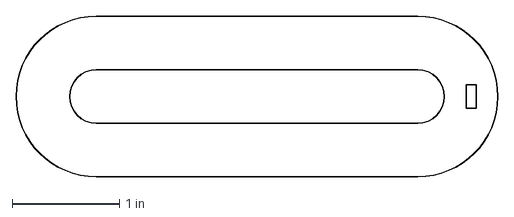
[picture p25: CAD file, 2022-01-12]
gear-depthing-gauge/Profile 1 (X2).dxf
4.50 x 1.50 in

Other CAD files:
angled-jigs/earth_jig_side_1.stl
cad/Gear Depthing Gauge.f3d
cad/Shaft Cutting Jig (for cutting flats).f3d
cad/Wood Cutting Layout.f3d

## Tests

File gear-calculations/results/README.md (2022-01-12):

Gear calculation results viewable on [Google Docs](https://docs.google.com/spreadsheets/d/1HO8HQtnuJBg7-cl2iLWuv1kIT8sFUn2m3BNM2MRiHnA/edit), copied here as a backup.

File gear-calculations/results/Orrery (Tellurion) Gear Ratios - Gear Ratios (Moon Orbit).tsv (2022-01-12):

Gears |  |  |  |  |  | Ratio | Target Ratio | Error (%) | Ang deviation in 100 years (deg) | Pitch Scaling (moon orbit) | First Stage Ratio | Target Perigee Regression | Target Perigee 2nd Stage Ratio | Best Perigee Gear Ratios |  | Ratio | Error (%) | Ang deviation in 100 years (deg) | Pitch Scaling (Perigee) | Target Nodes Regression | Target Nodes 2nd Stage Ratio | Best Nodes Gear Ratios |  | Ratio | Error (%) | Ang deviation in 100 years (deg) | Pitch Scaling (Nodes)
52 | 14 | 26 | 14 | 52 | 29 | 12.3687544 | 12.36874634 | 0.00006515058865 | 0.2900991978 | 0.7641509434 | 3.714285714 | 0.8870107566 | 0.2388105883 | 11 | 46 | 0.8881987578 | 0.1339331181 | 42.7680419 | 0.8636363636 | 1.053764597 | 0.283705853 | 15 | 53 | 1.051212938 | -0.2421469654 | -91.85972381 | 1.03030303
47 | 23 | 43 | 11 | 48 | 31 | 12.36873645 | 12.36874634 | -0.00007993625062 | -0.3559360346 | 0.6370967742 | 2.043478261 | 0.8870107566 | 0.4340690937 | 23 | 53 | 0.8867924528 | -0.02461117503 | -7.858935713 | 1.085714286 | 1.053764597 | 0.5156720368 | 16 | 31 | 1.054698457 | 0.08862133209 | 33.61896803 | 0.6714285714
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

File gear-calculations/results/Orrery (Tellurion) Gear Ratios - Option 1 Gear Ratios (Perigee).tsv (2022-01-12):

Moon Orbit Gear Train
49 | 12 | 34 | 10 | 49 | 55 |  | 13.88333333
Gears |  |  |  | Second Stage Ratio | Target Multiplier | Ratio | Target Ratio | Error (%) | Ang deviation in 100 years (deg) | Dist stage 1 | Dist Stage 2 | Pitch Scaling (stage 1) | Pitch Scaling (stage 2)
9 | 49 | 8 | 23 | 13.88333333 | 0.06389033062 | 0.8869565215 | 0.8870107566 | -0.00611436484 | -1.952343277 | 44 | 61 | 1.318181818 | 0.5081967213
8 | 49 | 9 | 23 | 13.88333333 | 0.06389033062 | 0.8869565215 | 0.8870107566 | -0.00611436484 | -1.952343277 | 44 | 61 | 1.295454545 | 0.5245901639
18 | 49 | 8 | 46 | 13.88333333 | 0.06389033062 | 0.8869565215 | 0.8870107566 | -0.00611436484 | -1.952343277 | 44 | 61 | 1.522727273 | 0.8852459016
16 | 49 | 9 | 46 | 13.88333333 | 0.06389033062 | 0.8869565215 | 0.8870107566 | -0.00611436484 | -1.952343277 | 44 | 61 | 1.477272727 | 0.9016393443
12 | 49 | 12 | 46 | 13.88333333 | 0.06389033062 | 0.8869565215 | 0.8870107566 | -0.00611436484 | -1.952343277 | 44 | 61 | 1.386363636 | 0.9508196721
9 | 49 | 16 | 46 | 13.88333333 | 0.06389033062 | 0.8869565215 | 0.8870107566 | -0.00611436484 | -1.952343277 | 44 | 61 | 1.318181818 | 1.016393443
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

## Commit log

2022-01-24 updated bom
    [Orrery BOM.tsv]
2022-01-24 orrery cad
